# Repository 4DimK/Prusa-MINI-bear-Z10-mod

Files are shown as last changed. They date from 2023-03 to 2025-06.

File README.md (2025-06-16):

# Since the release of Input Shaper for the MINI, this project is considered deprecated. Leaving it here in case of any interest.

# Prusa-MINI-bear-mod-Z10

## Table of Contents
1. [Introduction](#Introduction) 
1. [Features](#Features)
1. [Background](#Background)
1. [Disclaimer](#Disclaimer)
1. [Post MK4 release thoughts](#Post-MK4-release-thoughts)
1. [BOM](#BOM)
1. [Manual](#Manual)
1. [Firmware](#Firmware)
1. [Print profiles](#Print-profiles)
1. [License](#License)
1. [Credits and Inspiration](#Credits-and-Inspiration)

## Introduction

Bear mod adaptation with MK3S print-head for Prusa MINI(+). Based on 10mm Z rods.

## Features

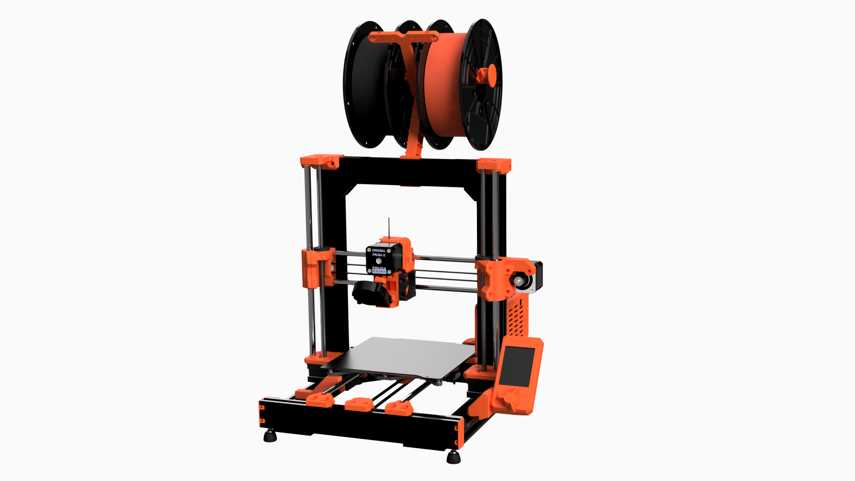
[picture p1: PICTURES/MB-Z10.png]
MB-iso


- Compatible with Prusa MINI and MINI+
- Supported (dual) Z-axis based on the stock 10mm rods
- MK3S printhead w/ Filament Sensor
- Reuse of as many non-printed parts as possible[^1]
- Increased frame robustsness
- Maintenance friendly
- Reduced noise levels
- Compatible with stock firmware (with few limitation, see [Firmware](#Firmware) section)
- Open-source

[^1]: Z rods are the only non-printed hardware part that will need to be modified and cut to length (311mm).

## Background

There are quite a few models and tutorials online (mainly in [Printables](https://www.printables.com/search/all?q=prusa%20bear%20mini)) to build your Prusa Mini Bear mod, but as soon as you try to dive into versions and part compatibility, it becomes chaotic. Before printing, I wanted to ensure that all parts are well aligned and compatible with each other, but as far as I could find, there was no published CAD version with a complete model. Either I had to make a collection and hope for the best, or work on my own remix.

Main issues I observed:

- X and Y belts not running parallel to the axis.
- No stock Prusa extruder R6 version with proper probe offsets.
- No CAD with 10mm Z rods to verify.
- Z rods where not properly aligned with X axis holders and top Z brackets.

To fix these, I did the necessary modifications to the Fusion 360 designs I could find (see credits), as well design several parts from scratch.

----

For the extruder, I started from the stock part as released by Prusa Research: https://github.com/prusa3d/Original-Prusa-i3

Parts that are not modified:

- Y-rod-holders, Y-idler-tensioner, 2040-end-caps (gregsaun) and cable clips: [Link](https://github.com/gregsaun/prusa_i3_bear_upgrade)

---

### Disclaimer

The Original Prusa MINI(+) is a great little printer and as far as I am concerned the print quality-to-value ratio is incredible for the price and ease of use. I chose to proceed with this build because as many others, I enjoy tinkering with 3D printers towards the possibility of improvement. In this case, towards a possibly more robust frame, which would (in theory at least) allow to maintain the same quality at higher accelerations with a direct-drive extruder to ease printing of flexible filaments. Keep in mind, as with any DYI assembly, there is always a chance of the final produced print quality to suffer, as it depends on the sourced hardware quality, part design and on the actual skills and experience put into building.

## Post MK4 release thoughts

- From the mechanical side it appears that the MK4 X axis + Nextruder combo (assuming it will be sold separately) should be directly applicable in this mod, due to the 10mm Z rods.
- Firmware wise, significant modifications may be needed for the automatic layer calibration and load-cell interfacing.
- Input shaping: At the time of writing, I am not aware of how to connect an accelerometer to the MINI Buddy board.

## Print settings

Assuming a Prusa MINI(+) is used, all parts are printed in PETG with the `0.2mm QUALITY@MINI `profile. The only applied changes are:

| setting | Value |
|--- | ----- |
| Perimeters | 3 |
| Infill density | 25% |

One exception from PETG is the print-head fan-shroud which is printed in ABS, using the same print settings.

## BOM

`To do`

## Manual

The following guides should provide most of the necessary steps. If there is further interest I will make another document for more specific details.

- Frame, Y and Z axis: [Bear Lab Guides](https://guides.bear-lab.com/c/BearFrame_Assembly_Guide)
- E axis: [Prusa MK3S assembly guide](https://help.prusa3d.com/guide/5-e-axis-assembly_169235)
- Z stepper motor in-series connection: [Split-Z-axis-for-MINI by 3DPGVA](https://github.com/3DPGVA/Split-Z-Axis-for-MINI/blob/master/2020-08-14_20h49_21.jpg)
    - The color coding matches the original Prusa MINI extruder motor. Follow it closely.
- Electronics: [Prusa MINI electronics assembly](https://help.prusa3d.com/guide/5-lcd-assembly-electronics_202703) - Step 19 for the overview of BUDDY board connections.

## Firmware

The goal of this mod is to make it compatible with the Original Prusa MINI(+) firmware, as to avoid the effort of maintaining a custom version.

Although the printer works directly after the mod, few features implemented at firmware level, are not compatible. Mainly, the `load/unload` scripts from the Filament section of the MINI screen.

Instead of using those, custom macros shall be used to perform load and unload filament actions. See [Print profiles](#Print-profiles) section.

The shortcoming is that these macros cannot be used while a job is running. If the filament runs out during a print, the factory default load/unload macros will be executed. That is fine for the unload function, but for the load phase I suggest to proceed as instructed in the screen **but** without actually inserting the filament to the extruder (only enough to register the filament with the sensor). Then only push the filament during the purging phase.

**Factory provided modifiable settings**

To properly use the MK3S printhead the following settings need to be changed directly from the MINI screen. 

Hint: The menu to change these is kind of hidden; to access select:

`Settings->HW Setup (Long press until sound)`:

| setting | Value |
|--- | ----- |
| Z-axis length | 210 |
| Extruder steps per unit | 140 |
| Extruder dir | Wrong |

Save and return.

## Print profiles

`Under construction`

Current draft versions under the PRINT_PROFILES folder.

Important: Make sure the any setting related to extrusion does not derive any values from the default MINI profiles. Even better, the MK3S settings are a good starting point.

In PrusaSlicer:
- `Printer Settings->Notes`: Make sure -PRINTER_MODEL_MINI- is changed to another value.
- `Filament Settings->Custom gcode`: Now that the printer name is changed, no bowden tuned values are applied. Since we use the MK3S extruder for this version. It is a good idea to copy-paste the settings from the equivalent MK3S filament profile.
- `Filament Settings->Dependencies`: Same as above. 

All of these are implemented in the exported config bundles within this repo.

## License

All parts are licensed under the GNU GENERAL PUBLIC LICENSE, Version 3. For more details please check the LICENSE file.

## Credits and Inspiration
- [Prusa Research](https://www.prusa3d.com/) for all their contributions to the 3D printing community and open-source 3D printers.
- [Grégoire Saunier](https://github.com/gregsaun) for his work on the [Prusa MK3S upgrade](https://github.com/gregsaun/prusa_i3_bear_upgrade), including the [Bear X axis](https://github.com/gregsaun/bear_extruder_and_x_axis). Additionally, credits are given to the original developers of the projects and products as cited by Grégoire Saunier. This readme file structure is also inspired by the same repo.
- [3DPGVA](https://github.com/3DPGVA) for his [Bear adaptation](https://www.printables.com/model/37939-prusa-mini-mk3s-bear-ultra-upgraded) for Prusa MINI and [Buddy board case](https://www.printables.com/model/36612-prusamini-buddy-board-case-for-mk3s-like).
- [Tomson](https://www.printables.com/social/88572-tomson/models?o=download_count) for providing the 10mm Z idler [source files](https://www.printables.com/model/64032-mini-bear-remixsmokistylewith-alternative-z-rod/files) I started with.

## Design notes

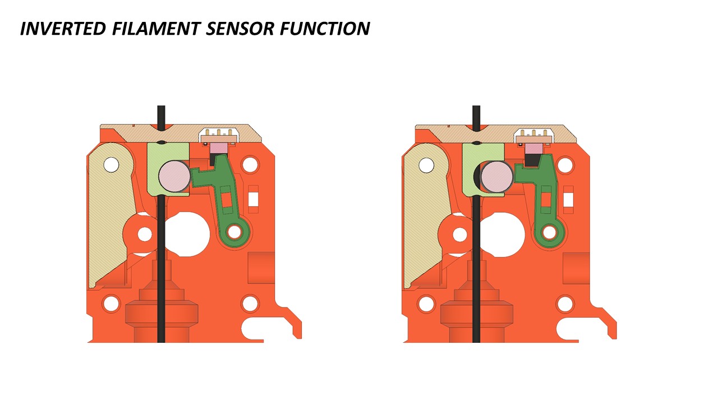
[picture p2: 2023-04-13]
PICTURES/FS.jpg

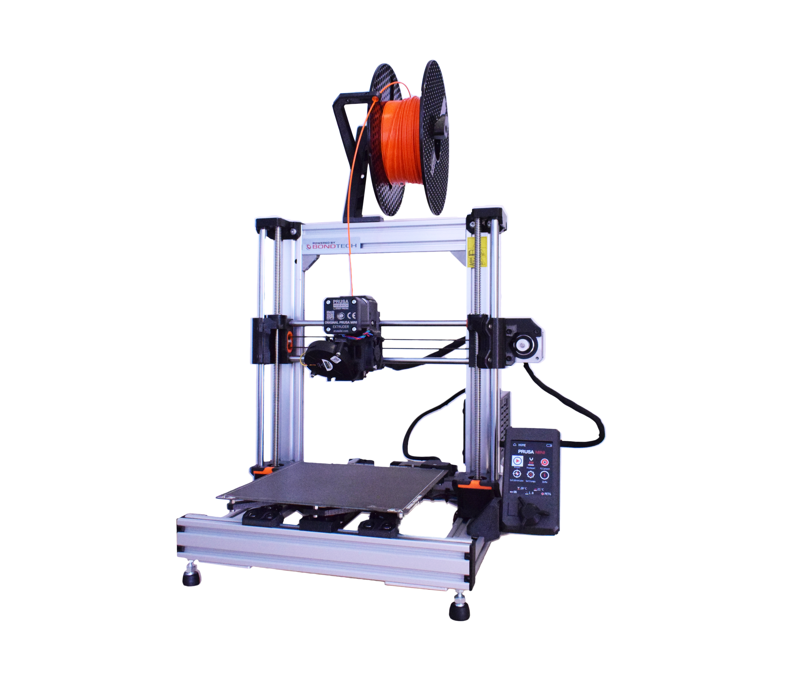
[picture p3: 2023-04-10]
PICTURES/ISO.jpg

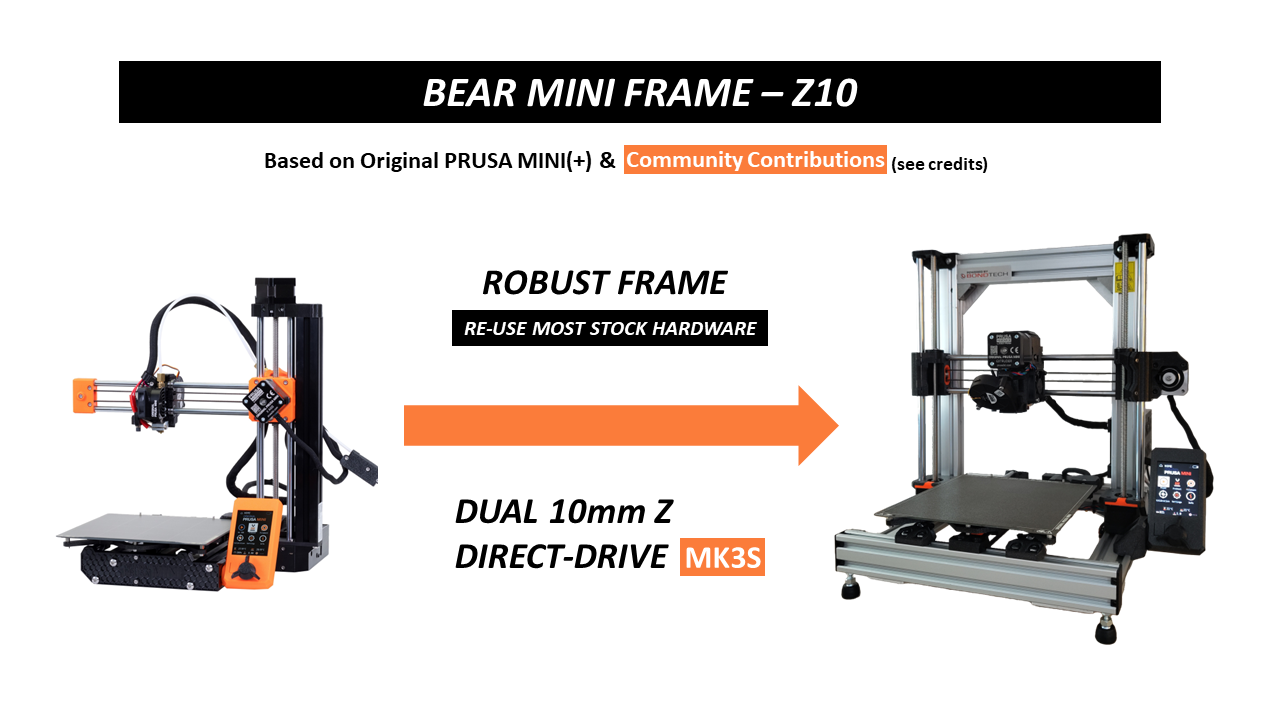
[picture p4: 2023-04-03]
PICTURES/cover.png

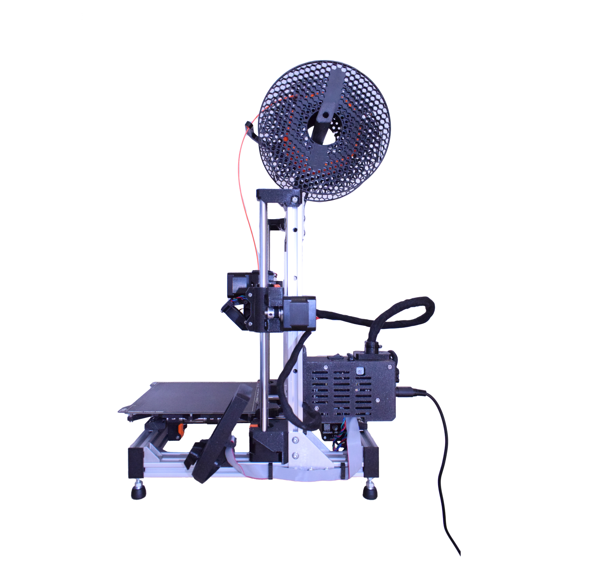
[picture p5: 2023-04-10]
PICTURES/SIDE.jpg

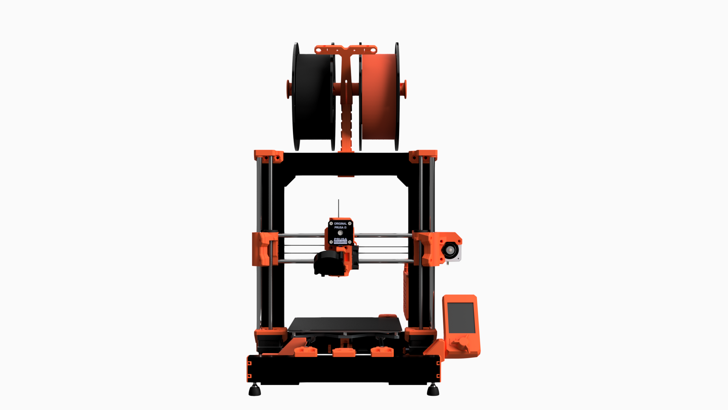
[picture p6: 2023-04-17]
PICTURES/CAD-FRONT.png

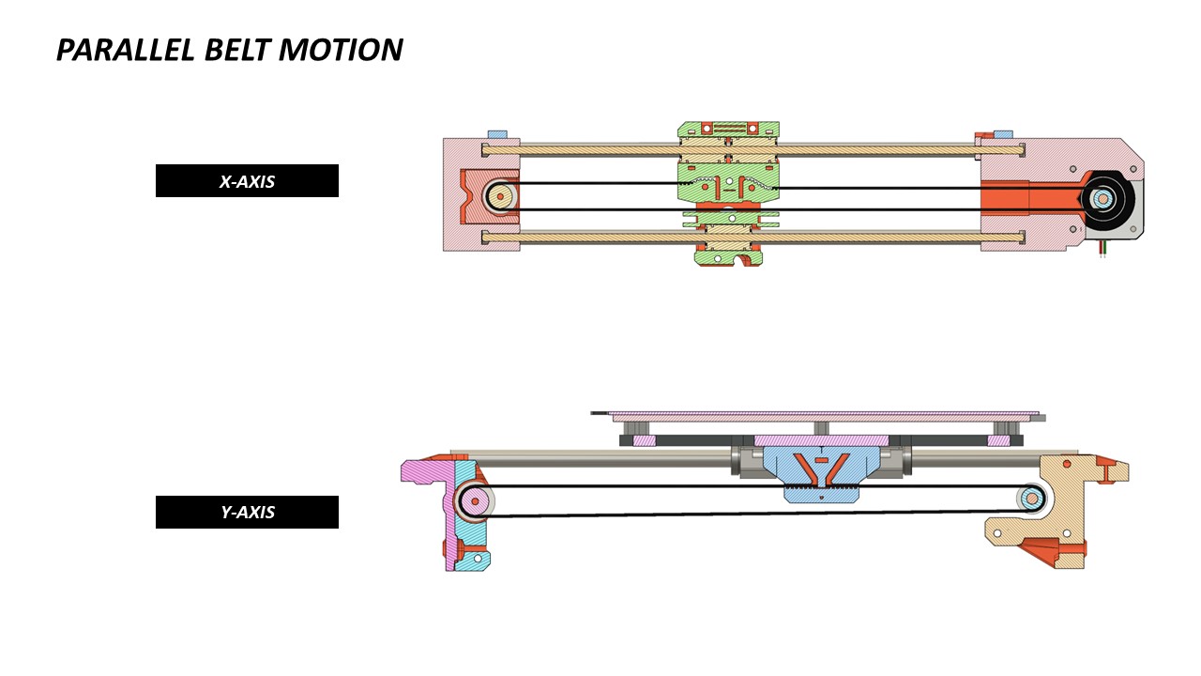
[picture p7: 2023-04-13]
PICTURES/BELTS.jpg

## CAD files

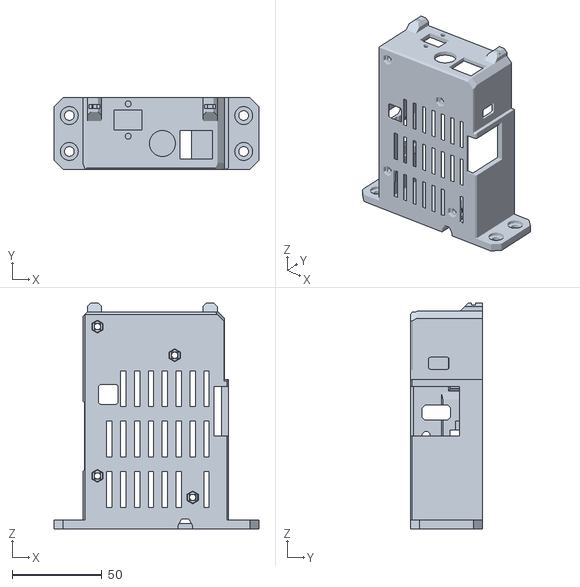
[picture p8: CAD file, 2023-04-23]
STL/electronics-parts/MB-electronics-case-main.stl
114.0 x 40.0 x 125.7

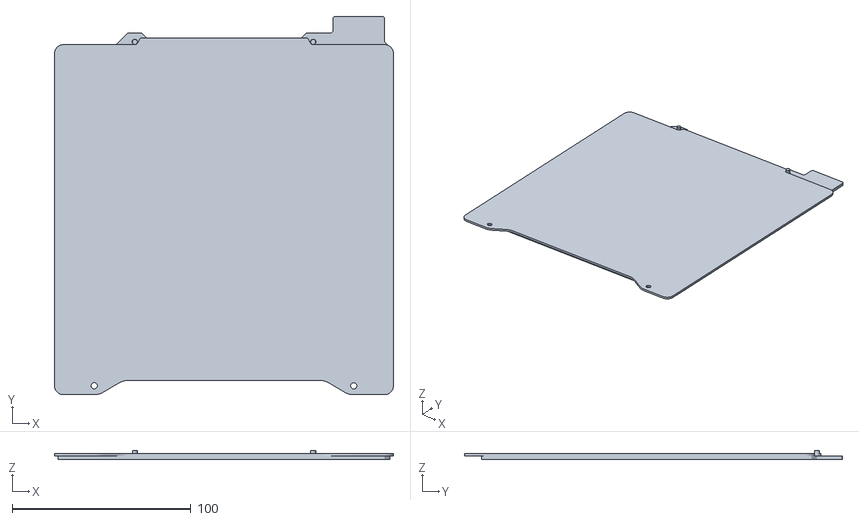
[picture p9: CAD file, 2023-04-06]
PRINT_PROFILES/mini_bed.stl
189.7 x 211.8 x 5.25

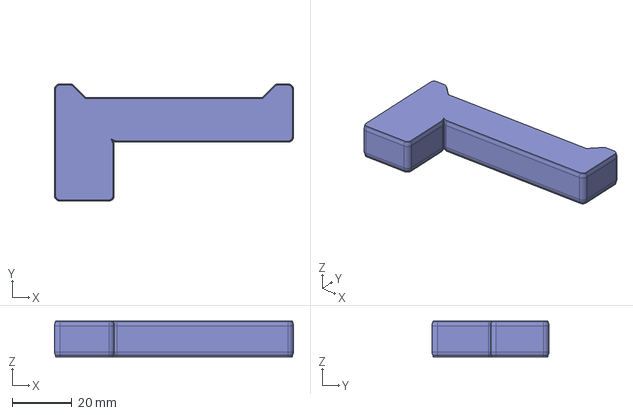
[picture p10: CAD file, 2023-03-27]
STEP/build-helpers/MB-build_helper_z_80mm.step
80.0 x 39.2 x 12.0 mm

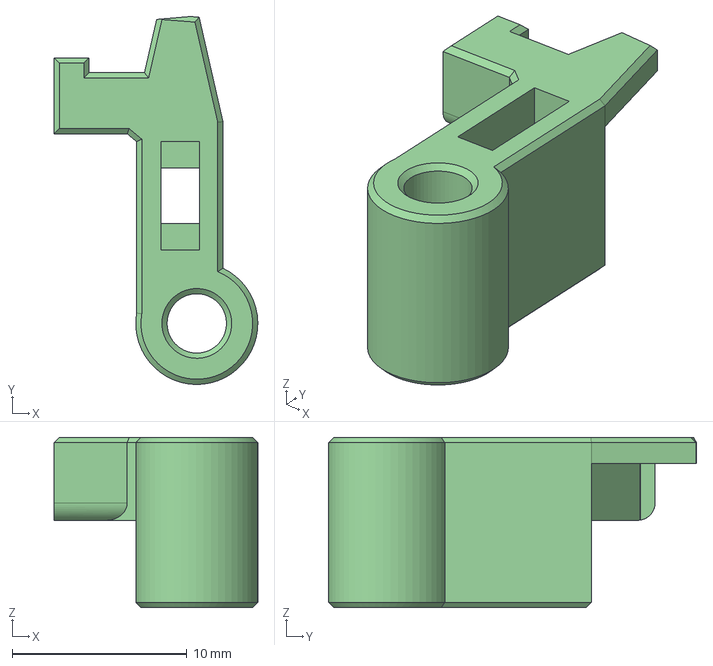
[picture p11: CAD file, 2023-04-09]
STEP/e-axis/MB-printhead.fs-lever-R6-IF.step
11.7 x 21.1 x 9.75 mm

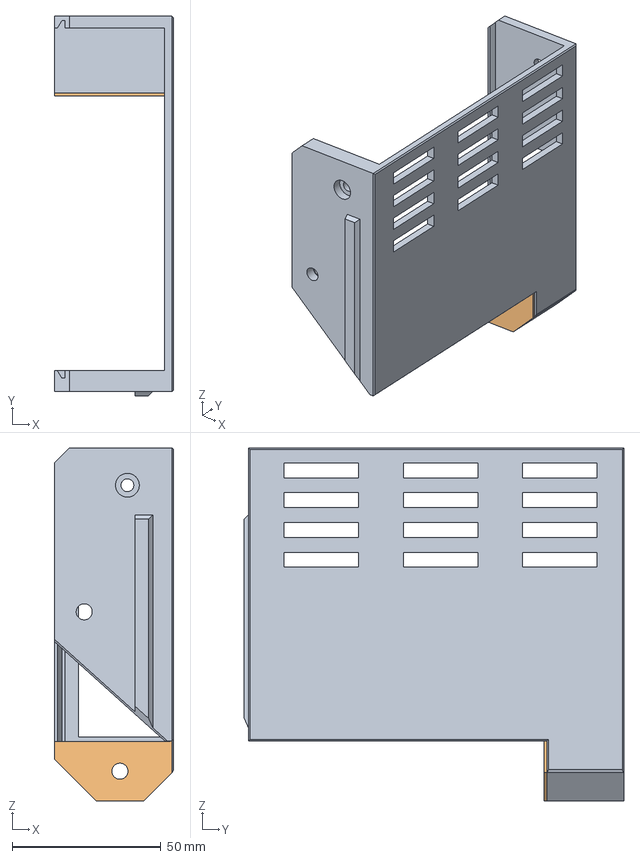
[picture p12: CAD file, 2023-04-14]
STEP/electronics-parts/MB-PSU-bottom-bracket.step
40.0 x 127.4 x 118.5 mm

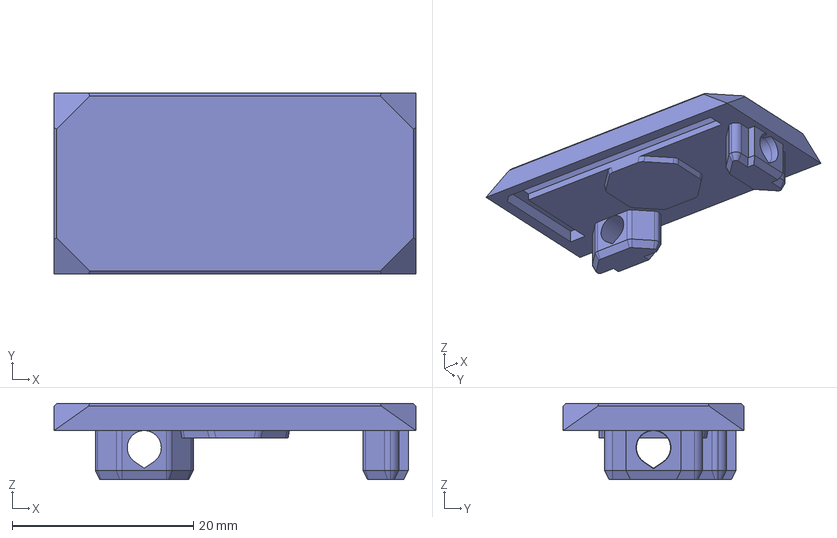
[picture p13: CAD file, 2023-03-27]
STEP/frame-parts/MB-end-cap-Z-left.step
39.9 x 19.9 x 8.40 mm

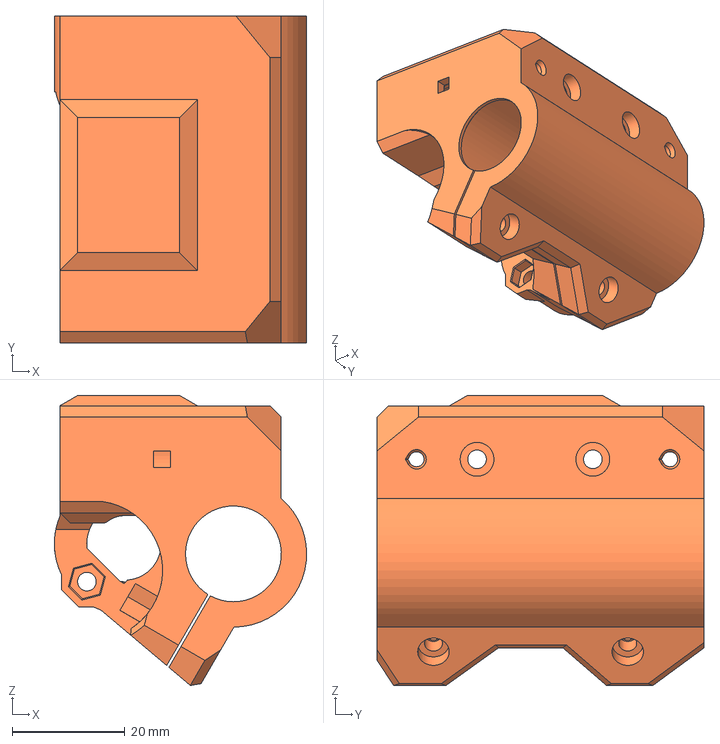
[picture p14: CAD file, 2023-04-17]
STEP/x-axis/MB-Z10.x-axis.MB-x-idler-left.step
44.8 x 58.0 x 51.5 mm

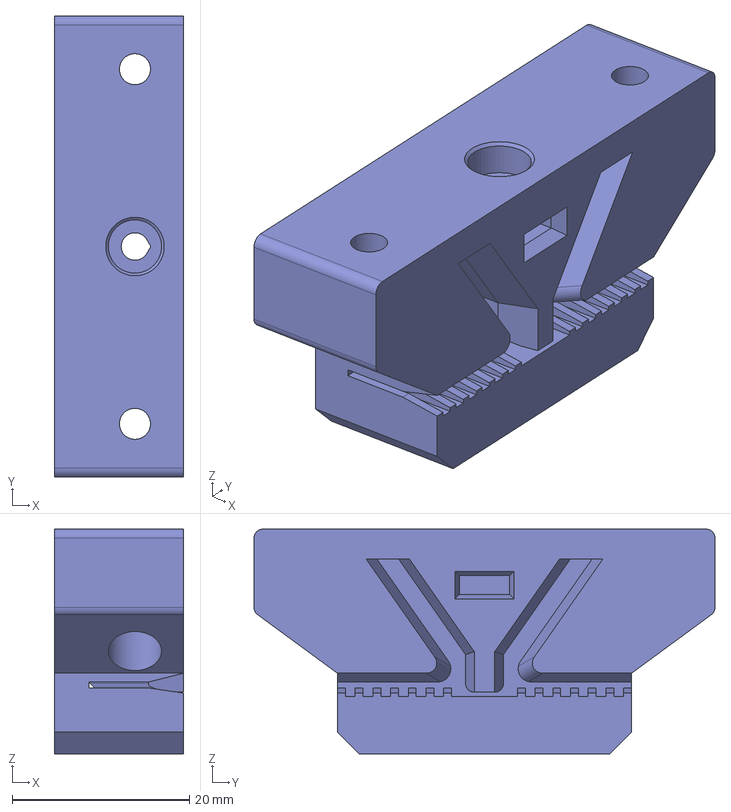
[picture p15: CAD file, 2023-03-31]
STEP/y-axis/MB-Z10.y-axis.MB-y-belt-holder.y_belt_holder.step
14.6 x 52.0 x 25.3 mm

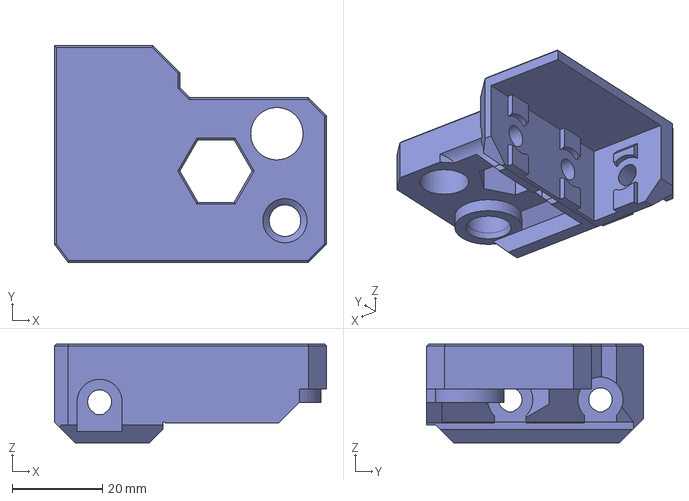
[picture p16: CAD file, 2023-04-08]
STEP/z-axis/MB-Z10.z-axis.MB-z-top-bracket-left.step
60.3 x 48.0 x 21.9 mm

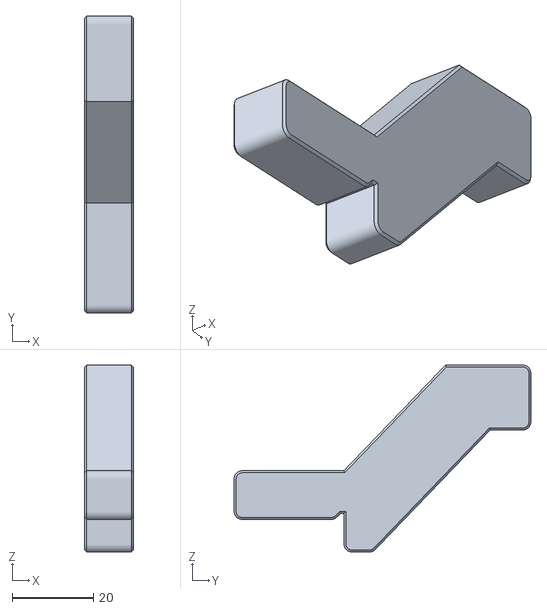
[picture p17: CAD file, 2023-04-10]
STL/build-helpers/MB-build-helper-y.stl
12.0 x 73.0 x 46.0

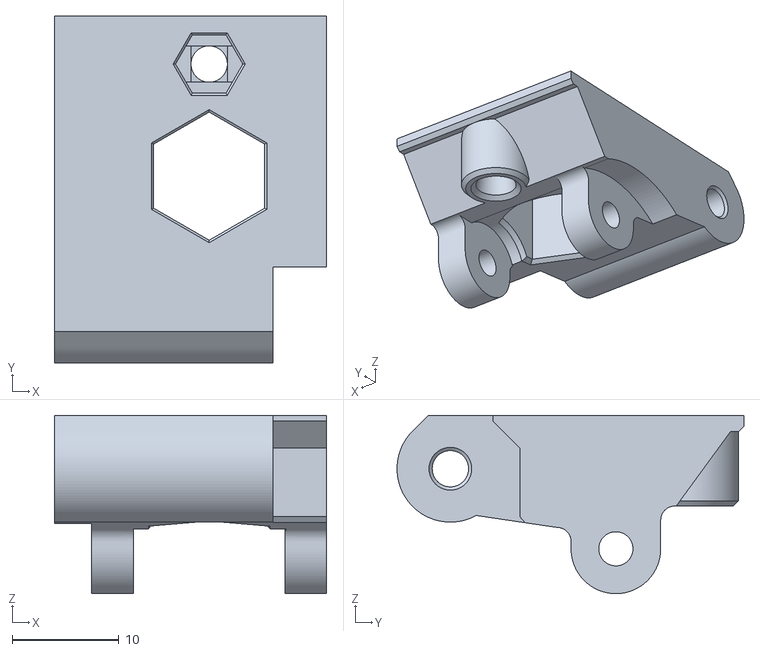
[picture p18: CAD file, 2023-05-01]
STL/e-axis/MB-extruder-idler-R6-mirrored-tight.stl
25.5 x 32.5 x 16.7

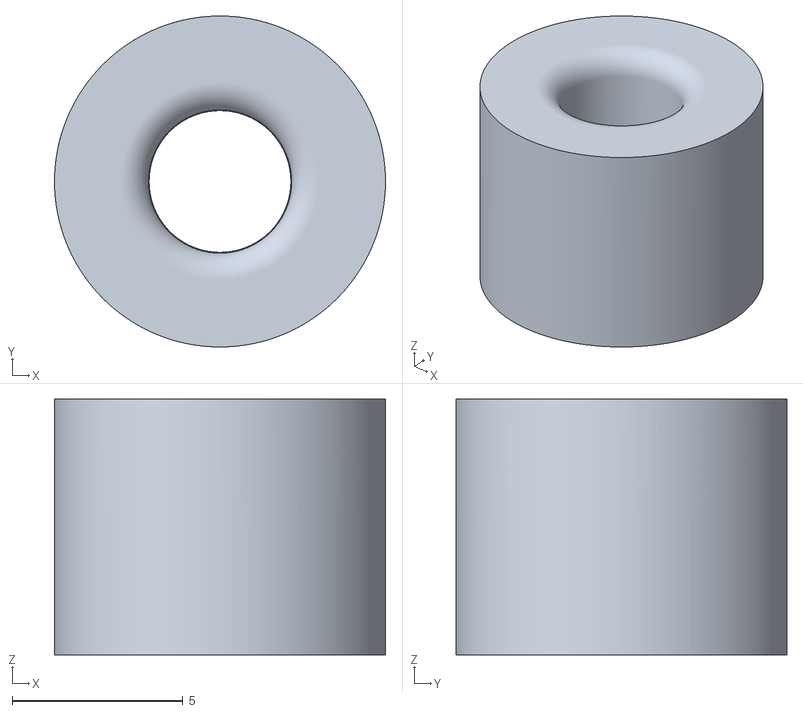
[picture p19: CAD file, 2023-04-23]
STL/frame-parts/filament-guide-PTFE-adapter.stl
9.70 x 9.70 x 7.50

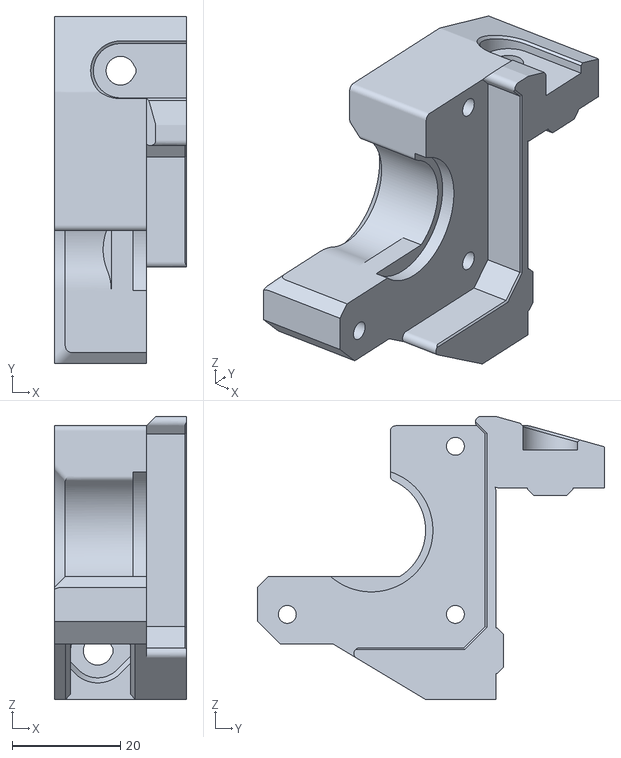
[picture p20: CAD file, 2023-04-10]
STL/y-axis/MB-y-motor-mount.stl
24.4 x 64.0 x 52.2

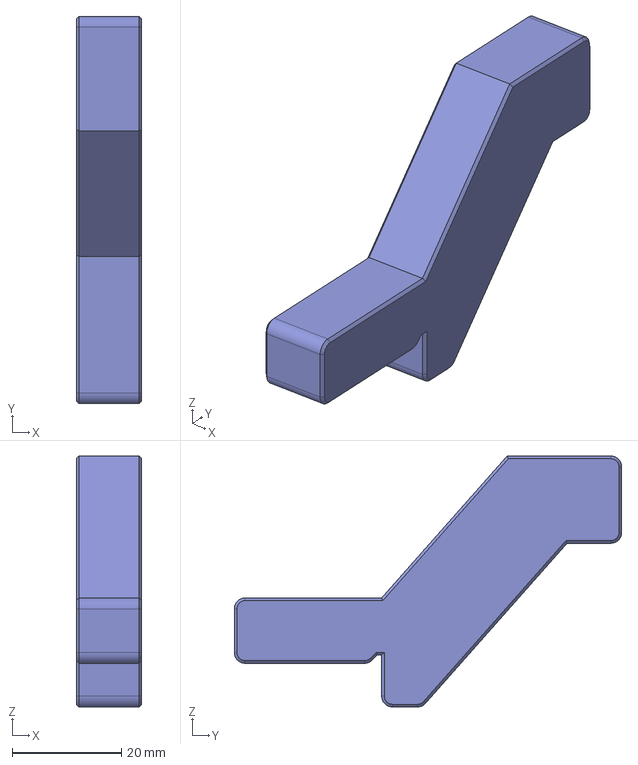
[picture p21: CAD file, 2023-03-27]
STEP/build-helpers/MB-build-heper-y.step
12.0 x 71.0 x 46.0 mm

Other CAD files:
STL/x-axis/MB-x-idler-left.stl
STL/z-axis/MB-z-top-bracket-left.stl
STEP/e-axis/MB-printhead.extruder-body-R6(MirrorEdit).step
STEP/electronics-parts/MB-display-clip.step
SOURCE/ASSEMBLY/MB-Z10-v1.3.f3z
STEP/e-axis/MB-printhead.MK3S-fan-shroud-R6(Mirror).step
STEP/e-axis/MB-printhead.adapter-printer-R6(Mirror).step
STEP/e-axis/MB-printhead.extruder-cover-R6(Mirror).step
STEP/e-axis/MB-printhead.extruder-idler-R6(Mirror).step
STEP/e-axis/MB-printhead.extruder-motor-plate-R6(Mirror).step
STEP/e-axis/MB-printhead.extruder-motor-plate-R6.step
STEP/e-axis/MB-printhead.fs-cover-R6(Mirror).step
STEP/e-axis/MB-printhead.fs-lever-R6(Mirror).step
STEP/e-axis/MB-printhead.print-fan-support-R6(Mirror).step
STEP/electronics-parts/MB-PSU-cover.step
STEP/electronics-parts/MB-PSU-top-bracket.step
STEP/electronics-parts/MB-Z10.electronics.MB-cable-clips.cable_clip_tft.step
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

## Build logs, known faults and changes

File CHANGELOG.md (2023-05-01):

# Change Log

## [v1.4] - 24/04/2023
### Fixed
- Readme E axis assembly link to MK3S+ instead of MK3S.

## [v1.3] - 24/04/2023
### Fixed
- MB-electronics-case:  Increasing the case thickness on all sides made it harder to attached the micro USB cable. Added a cutout that reduced the thickness in the connector area.

### Added
- PrusaSlicer configuration folders (tested).
- (optional) LED light bar front brackets with embedded hinge. Model in Printables [here](https://www.printables.com/model/460810-led-bar-front-hinged-prusa-bear).
- spool holder + (optional) filament guide, as found in Printables [here](https://www.printables.com/model/456501-2-spool-holder-mk3s-style-for-2040-profile)
- Extruder-idler STL that was missing.

## [v1.2] - 16/04/2023
### Changed
- CAD leadscrew is changed to a proper TR8x4(P2x2) as per [prusa3d](https://github.com/prusa3d/Original-Prusa-MINI/blob/master/DOCUMENTATION/ELECTRONICS/mini-motor-kit.pdf). The z-leadscrew-cap is designed based on that as to properly fit.
- Remixed the [*official* Prusa double spool holder](https://www.printables.com/model/418764-unofficial-official-prusa-i3-mk3s-spool-holder-not) as to snap into a 2020 extrusion and redesigned the handles from scartch as to make them 3D printable. Under testing.
    - This allows the use of the [new filament guide](https://www.printables.com/model/451501-mk4-printable-parts/files) as released with the MK4 by Prusa Research.
### Fixed
- Meanwell RSP320-24 PSU holder: fixed wrong PSU mounting whole diameter (was M3 instead of M4), increased thickness of cover plate. Redesigned the top bracket because it was using the wrong PSU mounting hole.
- Fixed changelog update dates.

## [v1.1] - 11/04/2023
### Changed
- Recolor CAD files as to better distinguish between frame (black) and printed (orange) parts.

### Added
- Meanwell RSP320-24 PSU holder. That should not be necessary for anyone already having a working MINI. Unfortunately I accidentally fried my PSU and I had to replace it with what I had laying around.

## [v1.0] - 09/04/2023
### Changed
- MK3S-extruder-body: Added bolt head cavity in the probe holder. 
- Spool-holder: Increased side diameter to easier insert M4 bolt.

### Fixed
- MB-FS-lever: adjusted gap for more reliable operation
- Increased overall robostuness of remixed electronics case

## [v0.9] - 08/04/2023
### Added
- Filament sensor functionality. The following parts are modified.
    - MB-extruder-motor-plate: Extra travel space is accommodated for the FS-lever inverted function.
    - MB-FS-lever: The lever is modified to provide the inverted (not mirrored) function of MK3S which complies with the MINI firmware sensor interpretation.
    - **Important** MK3S-extruder-body: The filament sensor cable provided for the MINI has inverted plug polarity when oriented to be used with the MK3S. The plug red and black wires need to be swapped. The part is edited to move mirror the plug alignment groove.
- MB-spool-holder is now extended with a filament guide, inspired from the images of the new MK4 holder. 

### Fixed
- X axis max travel was 3mm short (177mm). This is fixed by updating the 2040 top and front-rear profiles, to 220mm and 300mm respectively. This affects the following parts:
    - X-idler-right and left: X-axis rod cavities are shortened by 2mm each.
    - MB-helper-Y: Length increased by 2mm.
    - X axis belt lenght: 4mm of extra length is required.
- Z-top-bracket: The tolerance is increased from 0.2mm to 0.25mm to allow easier rod insertion. Also, following from the aforementioned combination of the bracket with the end-cap, the extra thickness allows some room for Z rod length mismatches (in case the rods are cut manually).
- X-axis-endstop-spacer is not extended to sit on top of the right idler. This effectively constrains the spacer from rotating. The spacer also does not limit the tramming function.
    - The spacer provides 3.5mm of clearance. Just enough to not tram to the leadscrew. This can easily be incorporated within the idler itself. The reason to not do that is that in case another extruder design is used, the required clearance might be different, or not at all.

### Changed
- Top Z endcaps and Z-top-brackets are now a combined part. This results in a more robust bracket that can also be used to tram align the X axis.
- In MK3S-extruder-body, the probe has been brought 3mm close to the extruder. 
- MB-display-holder: added extra thickness around the M3 bolt as to allow insertion of a M3 locknut.
- MB-electronics case: This is now a complete remix of the original design from 3DPGVA. The reason is that there was not enough space to incorporate the extra length of the wires I had and the lead was not closing properly. I took the change to add extra cable covers, inspired both from MK3S as well as the MK4 electronics boxes.

## [v0.81] - 06/04/2023
### Added
- X-axis-endstop-spacer. The x axis idlers are to be updated as to avoid sensorless homing by side kicking the leadscrew. For versions prior to v0.81 it is recommended to use the spacer on the top X axis rod attached next to right idler as to avoid damaging the Z leadscrew.
- MB-spool-holder. This is a draft version and is not printed yet. Not even sure if I will be using a top place spool holder. Either way, this remixed out of PR supplied MK3S STL of their spool holder and modded to be attached on 2020 extrusion. There is also an insert with space for M4 bolt. That is meant to incorporate a filament guide.
- Added PRINT_PROFILES folder. Currently it includes a draft config bundle with only one Bear compatible profile (settings, filament and printer) derived from 0.2mm QUALITY @MINI for 0.4mm nozzle. All settings related to the extruder are copied from the equivalent MK3S profile. STL and SVG of ht the MINI heatbed are included if adding the visuals is of interest. These are directly downloaded from PrusaSlicer github [repo](https://github.com/prusa3d/PrusaSlicer/tree/master/resources/profiles/PrusaResearch).

## [v0.8] - 02/04/2023
### Added
- Pictures of the realized mod

### Changed
- Updated STL files for the following parts:
    - X-idler-left
    - X-idler-right

### Fixed
- X-idler-right and X-idler-right linear rod cavities for x-axis linear rods is shortened to meet the length of the stock rods for easy assembly.

## [v0.33] - 31/03/2023
### Fixed
- X-idler-right and X-idler-left bearing holes length is extended by 0.4mm as to make sure that the bearing sits below the top surface and not interfering with the POM nut. Also, a chamfer is added to it to ease the overhand printing.
- Y-belt-holder for the mini needs to allow room for the PCB heater center bolt head. A 6x3mm cavity is added in the center hole.
- CAD length of X-axis linear rods as taken from the original CAD I started with, is not in accordance with the stock rods. The length is fixed to 279mm. To make sure that both rods are symmetrically inserted between the idlers, 18mm bolts need to be fully inserted in the left idler.

## [v0.32] - 30/03/2023
### Fixed
- Y-motor-mount top surface was barely blocking the headbed rear bold head. Reduced thickness by 1mm to allow free move.
- Z-motor-mount hole for the 10mm rod had no tolerance applied. It is now set at 0.2mm.
- Z-top-bracket had a tolerance for 10mm rod set 0.085mm. That proved to small for my Mini. It is now also increased to 0.2mm.

## [v0.31] - 29/03/2023
### Changed
- Reduced and rounded Z rod length. Total axis travel possible is 206mm. Albeit, without changing the firmware max travel is set at 180mm from the bed surface.

## [v0.3] - 27/03/2023
### Changed
Realized that MK3S and Prusa MINI use different leadscrew specifications, hence gregsaun's leadscrew caps are not compatible with this mod. 
- Designed and tested new MINI(+) compatible leadscrew caps for TR8x4(p2x2) as per [Prusa MINI motor specifications](https://github.com/prusa3d/Original-Prusa-MINI/blob/master/DOCUMENTATION/ELECTRONICS/mini-motor-kit.pdf). Part tolerance is set to 0.2 mm, which should work well with any well working MINI(+). 

If you need different tolerance just adjust the `OffsetFaces` feature in Fusion. 

## [v0.25] - 25/03/2023
### Added
- gregsauns Bear Z motor leadscrew caps and cable clips. Updated sources files.

## [v0.24] - 24/03/2023
### Added
The T-nuts I had in stock appeared to have a difficulty tightening and fixing the component to the profile. 
- Added an additional cut in the v-slot groove (of all relevant parts) as to provide some extra turns.

## [v0.23] - 23/03/2023
### Added
- T-slot groove for MB-z-top-bracket and MB-z-motor-bracket since I accidentally used T-slot profiles for my Z axis. This feature is grouped in Fusion360 files and suppresses to leave V-slot groove for default.
### Fixed
- In MB-z-motor-bracket added a fillet in the motor entry slot, as to ease side insertion with a slight push. This is because there is no room to insert the motor from underneath after the bracket is fixed in place.

## [v0.22] - 21/03/2023
### Fixed
My Mini+ Z threaded rod length was measured to be 309mm, which is different from the ones present in the CAD I started with (it safe to say now that the entire CAD has been modified). This affects the Z 2040 profile as well as the 10mm linear rod length. 
- Z profiles are now adjusted to a more reasonable length of 349mm and the linear rod properly adjusted as well to 311mm.

## [v0.21] - 18/03/2023
### Added
- Build-helpers (remixed from gregsaun's Prusa Bear). One to set the Y-rod distance and the other for the Z-profile distance. 

## [v0.2] - 12/03/2023
### Fixed
- Modified the MK3S Bear Y-motor-mount as to allow maximum Y travel for the Mini. 
- Z axis profiles y-axis offset at the position to allow full cover of print-bed. 
- Further stitching of internal gaps of MB-x-idler-right.

## [v0.14] - 11/03/2023
### Added
- Bolt head slot in Z-motor-brackets. 
### Fixed
- Updated Z-top-brackets to fix rod center misalignment introduced after  Z-motor-mount alignment fix.
- Cleaned up source CAD files and uploaded pre-printing state .f3z and .step files.

## [v0.13] - 10/03/2023
### Changed
- STEP file clean up and orient with Z upwards.
- Changed Y-motor-mount to the one shared by gregsaun ([link](https://github.com/gregsaun/prusa_i3_bear_upgrade)) as it seems more robust and provides better contact with the motor surface.
### Fixed
- Fixed internal gaps within parts, at least the ones I accidentally found.

## [v0.12] - 09/03/2023
### Added
- Added display holder and remaining electronics. 
- Added end caps in assembly, as they were provided by gregsaun.
### Fixed
- Fixed Y axis belt holder alignment. 
- Organized STEP assembly, assigned proper names to all components.

## [v0.11] - 08/03/2023 
### Fixed
- Fixed slight misalignment of X axis belt by raising the idler side belt lock system by 0.52mm. 

## [v0.1] - 07/03/2023 
Initial upload.

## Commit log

2023-03-27 initial test + structure
    [MB-2020-corner-bracket.stl, MB-buddy-board-capBed.stl, MB-buddy-board-case.stl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]
2023-03-27 readme update
    [MB-adapter-printer-R6-mirrored.stl, MB-extruder-cover-R6-mirrored.stl, MB-extruder-motor-plate-R6-mirrored.stl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]
2023-03-27 STL folder restructuring
    [MB-2020-L-bracket.stl, MB-adapter-printer-R6-mirrored.stl, MB-buddy-board-capBed.stl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]
2023-03-27 STEP parts, readme & changelog update
    [MB-Z10.electronics.MB-cable-clips.cable_clip_tft.step, MB-Z10.electronics.MB-cable-clips.cable_clip_vertical.step, MB-Z10.electronics.MB-display-holder.step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]
2023-03-27 Added printhead cable holder stl. Readme update
    [MINI-display-box.stl, MK3S-cable-holder-R6.stl]
2023-03-30 assembly fixes for Z and Y printed parts
    [MB-Z10.y-axis.MB-y-motor-mount.step, MB-Z10.z-axis.MB-z-motor-bracket-left.step, MB-Z10.z-axis.MB-z-motor-bracket-right.step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]
2023-03-30 old assembly files cleanup
2023-03-31 X and Y axis part fixes. Changelog & readme update
    [MB-Z10.x-axis.MB-x-idler-left.step, MB-Z10.x-axis.MB-x-idler-right.step, MB-Z10.y-axis.MB-y-belt-holder.y_belt_holder.step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]
2023-04-03 Realized mod pictures and file updates. Changelog & readme update
    [MB-Z10.x-axis.MB-x-idler-left.step, MB-Z10.x-axis.MB-x-idler-right.step, MB-x-idler-left.stl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]
2023-04-03 clean old assembly files versions
2023-04-06 Added print profiles, x-axis homing spacer, spool holder. Updated Changelog and readme.
    [MB-spool-holder.stl, MB-x-endstop-spacer.stl, mini_bed.stl]
2023-04-08 filament sensor, probe offset reduced, new z-top brackets, new electronics box, new spool holder. Changelod and readme update
    [MB-Z10.x-axis.MB-x-idler-left.step, MB-Z10.x-axis.MB-x-idler-right.step, MB-Z10.z-axis.MB-z-top-bracket-left.step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]
2023-04-09 v1.0 finalizations. Changelod update
    [MB-buddy-board-capBed.stl, MB-buddy-board-case.stl, MB-buddy-board-cover.stl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]
2023-04-13 Add Meanwell RSP320-24 PSU holder. CAD recolor. Changelog update
    [MB-PSU-bottom-bracket.stl, MB-PSU-bracket.iges, MB-PSU-cover.stl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]
2023-04-14 Updated alternative PSU (RSP320-24) holder. Extended display cable clip length.
    [MB-PSU-bottom-bracket.step, MB-PSU-bottom-bracket.stl, MB-PSU-cover.step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]
2023-04-14 PSU holder fixes & Changelog update.
    [MB-PSU-bottom-bracket.step, MB-PSU-bottom-bracket.stl]
2023-04-17 PSU holder fixes, Prusa double-spool-holder remix. Changelog & readme update.
    [MB-filament-guide.step, MB-filament-guide.stl, MB-spool-holder-base-part1.stl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]
2023-04-17 v1.2 step and source assembly files upload
2023-04-17 Updated left and right X-idler STL and STEP to v1.2
    [MB-Z10.x-axis.MB-x-idler-left.step, MB-Z10.x-axis.MB-x-idler-right.step, MB-x-idler-left.stl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]
2023-04-23 moved source assembly to LFS, added new spool holder and led lights. Fixed electronics case and more
    [MB-electronics-case-main.stl, MB-extruder-idler-R6-mirrored.stl, filament-guide-PTFE-adapter.stl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]
2023-04-23 old version cleanup
    [MB-Z10-v1.3.f3z]
2023-04-23 removed accidental inclusion of physical printer profile
2023-05-01 fixed e-axis manual link (point to MK3S+ and not MK3S
    [MB-extruder-idler-R6-mirrored-tight.stl, MB-fs-cover-R6-mirrored-extra-space.stl]
